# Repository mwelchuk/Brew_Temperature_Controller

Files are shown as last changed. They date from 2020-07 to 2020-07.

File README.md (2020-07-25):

# Brew Temperature Controller

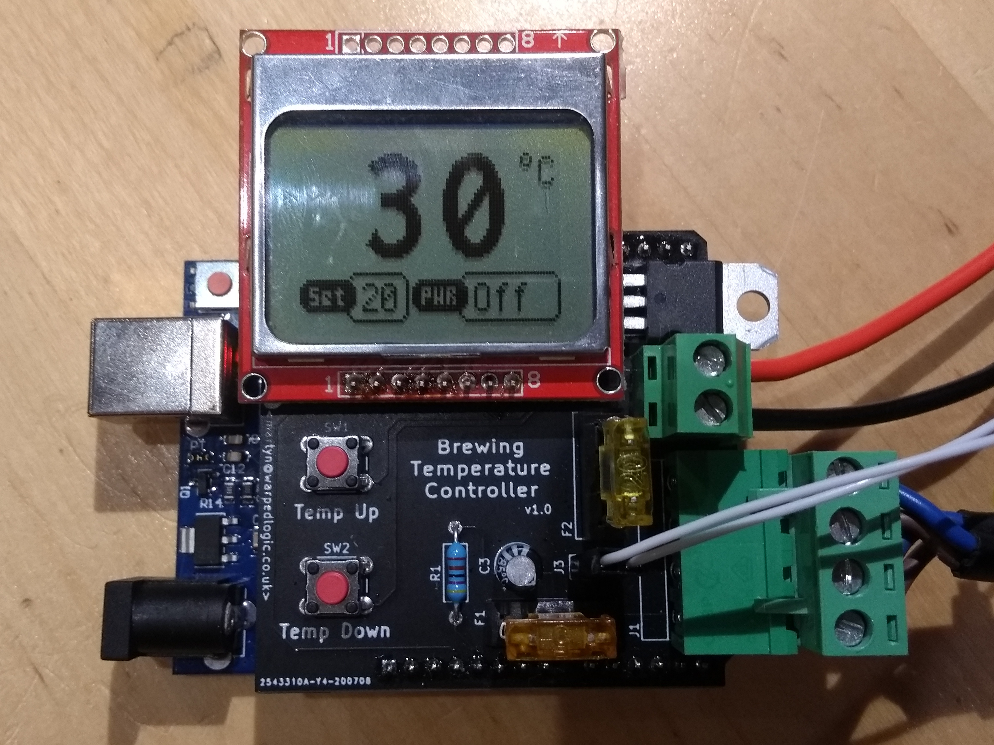
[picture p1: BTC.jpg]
Brew Temperature Controller


This project is a small heater controller that I have made to enable a few spare 3D printer parts I had lying arround to be used to control the temperature of my beer when brewing. I had been using a full RAMPS1.4 controller with a 4 line display, but this was very bulky. Rather than the Arduino Mega utilised with the RAMPS board, this uses an Arduino Uno, which is much smaller.

The device is fully powered from the PSU that's needed to supply power to the heater (this can not be pulled from the Arduino). If plugged in via USB, the set temperature, power output (scaled from 0-255) and current temperature are logged approximately once a second.

## PCB Ideas

- Improve layout of MOSFET now a more powerful transistor is being used.
- Getting noise back in (cheap) power supply, better smoothing?

## Code Ideas

- Better PID library

## Parts

- Parts below from CPC (cpc.farnell.com):

```
Order Code	Qty	Manufacturer Part Number	Manufacturer / Description									Line Price Ex. VAT (Inc. Vat)
SW02467		2	MCDTS6-1R			MULTICOMP PRO  Switch, Tactile 4.3mm 260g							0.22
CN21011		1	CTBP9358/4			CAMDENBOSS  5.08mm Horizontal Pluggable Terminal Block Header, 4-Pole, 15A			0.43
CN19453		1	CTB0708/2			CAMDENBOSS  PCB Terminal, High Power, 5.08mm, 2 Way						0.49
FF02092		2	MCCQ-122			MULTICOMP PRO  Fuseholder, PCB Mount, Mini Blade						0.48
CA08185		1	MCMR50V106M5X7			MULTICOMP PRO  Electrolytic Capacitor, 10 µF, 50 V, MCMR Series, ± 20%, Radial Leaded, 5 mm	0.05
SC11131		1	STP60NF06L			STMICROELECTRONICS  Power MOSFET, N Channel, 60 V, 60 A, 0.014 ohm, TO-220, Through Hole	1.36
```

- Nokia 5110 style screen with the following pinout:

```
Pin	Use
1	RST
2	CE
3	DC
4	DIN
5	CLK
6	VCC
7	LIGHT
8	GND
```

- Arduino Uno, cheap clone used
- Fuses: Standard Car mini Fuses. Used 5A (smallest I had) for electronics, 20A for heater output.
- Heater I found a standard 22cm circular 3D printer heated bed fits nicely under my brew bucket (it was this that inspired the build).
- Thermistor: Standard 100K thermistor, as used on many 3D printers.
- PSU: Currently using spare 0.8A 12v PSU as might be used on a small 3D printer.

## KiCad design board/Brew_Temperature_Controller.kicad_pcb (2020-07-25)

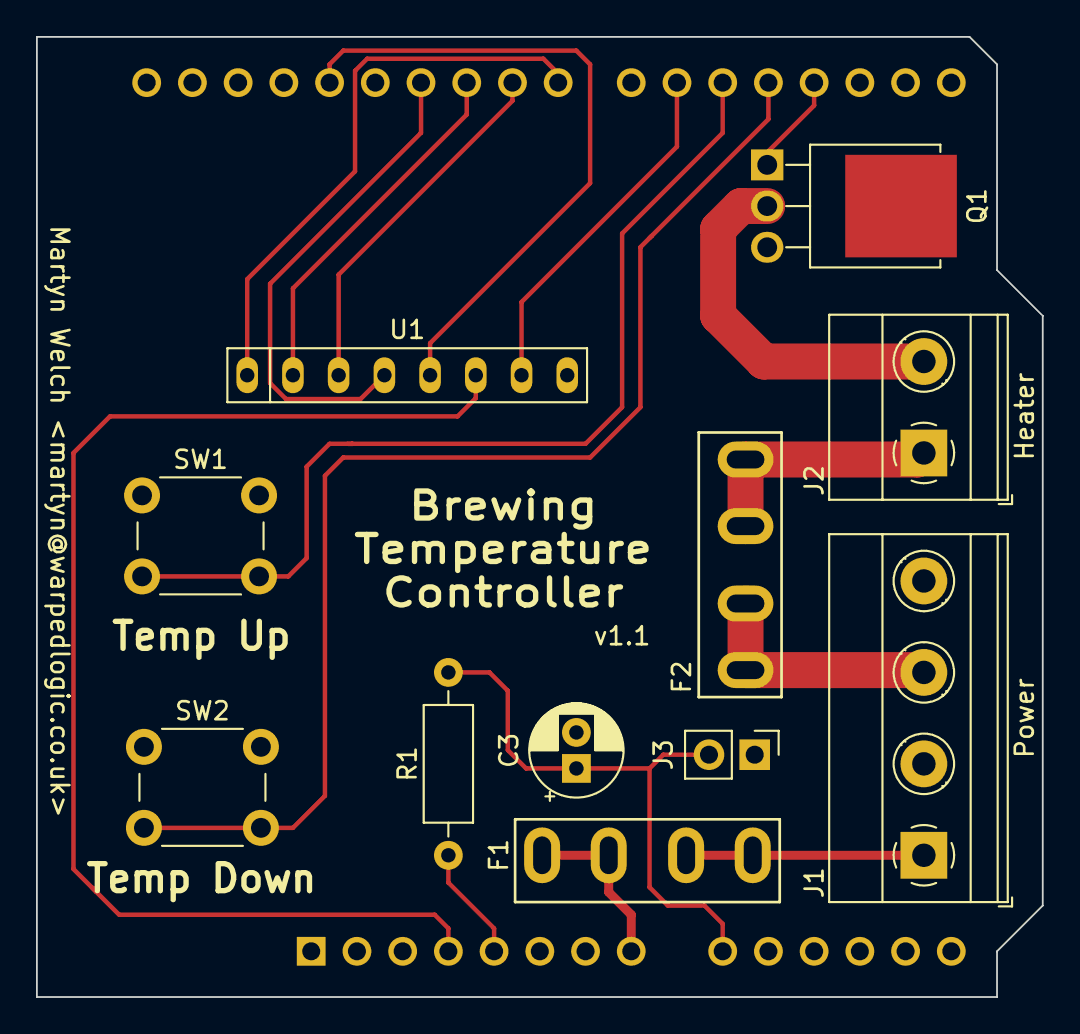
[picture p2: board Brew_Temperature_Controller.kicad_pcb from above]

Board: 2 copper layers, 55.9 x 53.3 mm, 12 parts (1 on the bottom side), 18 nets.

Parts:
A1: Arduino_UNO_R3
C3: 10uF; CP_Radial_D5.0mm_P2.00mm
F1, F2: MCCQ-122
J1: CTBP9358/4; TerminalBlock_Phoenix_MKDS-1,5-4-5.08_1x04_P5.08mm_Horizont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
J2: CTB0708/2; TerminalBlock_Phoenix_MKDS-1,5-2-5.08_1x02_P5.08mm_Horizont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
J3: Conn_01x02_Male; PinHeader_1x02_P2.54mm_Vertical
Q1: IRLU024NPBF; TO-251-3-1EP_Horizontal_TabDown
R1: 4K7; R_Axial_DIN0207_L6.3mm_D2.5mm_P10.16mm_Horizontal
SW1, SW2: MCDTS6-1R; SW_PUSH_6mm_H4.3mm
U1: Nokia_5110_Module

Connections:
+3V3: A1.4, U1.6
+5V: A1.5, R1.1
+12V: A1.8, F1.1
Button1: A1.20, SW1.2
Button2: A1.19, SW2.2
CE: A1.25, U1.2
DC: A1.24, U1.3
GND: A1.6, A1.7, A1.29, C3.2, J1.2, J1.4, J3.1, Q1.3, SW1.1, SW2.1, U1.8
HEATER: A1.18, Q1.1
LIGHT: A1.21, U1.7
unnamed: F1.2, J1.1
unnamed: F2.2, J1.3
unnamed: J2.2, Q1.2
RST: A1.23, U1.1
SCLK: A1.28, U1.5
SDIN: A1.26, U1.4
THERM: A1.9, C3.1, J3.2, R1.2
Vdrive: F2.1, J2.1

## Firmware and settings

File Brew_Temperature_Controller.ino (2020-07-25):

/*
 * Brewing Temperature Controller
 * 
 * Copyright (C) 2020 Martyn Welch <martyn@warpedlogic.co.uk>
 * 
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
 * You should have received a copy of the GNU General Public License
 * along with this program; if not, write to the Free Software
 * Foundation, Inc., 51 Franklin Street, Fifth Floor, Boston,
 * MA  02110-1301, USA.
 */

/*
 * The following libraries are used:
 * - NTC Thermistor (MIT): https://github.com/YuriiSalimov/NTC_Thermistor
 * - U8g2 (2-Clause BSD): https://github.com/olikraus/u8g2
 * - FastPID (LGPL v2.1): https://github.com/mike-matera/FastPID
 */

#include <Arduino.h>
#include <U8g2lib.h>
#include <Thermistor.h>
#include <NTC_Thermistor.h>
#include <FastPID.h>
#include <EEPROM.h>

#ifdef U8X8_HAVE_HW_SPI
#include <SPI.h>
#endif
#ifdef U8X8_HAVE_HW_I2C
#include <Wire.h>
#endif

#define SWITCH_1 5
#define SWITCH_2 4
#define THERM_PIN A0
#define LIGHT_PIN 6
#define OUTPUT_PIN 3

#define REFERENCE_RESISTANCE   4700
#define NOMINAL_RESISTANCE     100000
#define NOMINAL_TEMPERATURE    25
#define B_VALUE                3950

#define DEBOUNCE_PERIOD 1000

#define LIGHT_PERIOD 2000
unsigned long light_time = 0;

float Kp=25, Ki=0.2, Kd=0.01, Hz=37;
int output_bits = 8;
bool output_signed = false;

FastPID myPID(Kp, Ki, Kd, Hz, output_bits, output_signed);

U8G2_PCD8544_84X48_F_4W_SW_SPI u8g2(U8G2_R0, /* clock=*/ 13, /* data=*/ 11, /* cs=*/ 10, /* dc=*/ 9, /* reset=*/ 8);  // Nokia 5110 Display

unsigned long debounce_switch_1 = 0;
unsigned long debounce_switch_2 = 0;

#define SETMAX 40
#define SETMIN 0
int setpoint = 25;
char setchar[4];
#define NUM_TEMPS 20
double temps[NUM_TEMPS];
int temp_cnt = 0;
int current = 69;
char curchar[4];
uint8_t output = 0;
char outchar[5];
unsigned long log_time;

int state1;
int hold1 = 0;
bool change1 = true;

int state2;
int hold2 = 0;
bool change2 = true;

Thermistor* thermistor;

#define SAVE_MAGIC 0xbe
#define SAVE_ADDRESS 0
struct saved_state {
  int magic;
  int temp;
};

struct saved_state saved;

void setup(void) {

  u8g2.begin();

  Serial.begin(115200);

  pinMode(SWITCH_1, INPUT_PULLUP);
  pinMode(SWITCH_2, INPUT_PULLUP);
  pinMode(LIGHT_PIN, OUTPUT);
  digitalWrite(LIGHT_PIN, HIGH);
  pinMode(OUTPUT_PIN, OUTPUT);
  digitalWrite(OUTPUT_PIN, LOW);

  thermistor = new NTC_Thermistor(
    THERM_PIN,
    REFERENCE_RESISTANCE,
    NOMINAL_RESISTANCE,
    NOMINAL_TEMPERATURE,
    B_VALUE
  );

  Serial.println("Setpoint, Output, Temperature");

  EEPROM.get(SAVE_ADDRESS, saved);

  if (saved.magic == SAVE_MAGIC) {
    setpoint = saved.temp;
  } else {
    saved.magic = SAVE_MAGIC;
  }

}

/*
uint8_t bitmap[] = {0x3F, 0xFF, 0xA5, 0xA5, 0xA1, 0xE1, 0x21, 0x1E};
*/
void refresh_display(char *curchar, char *setchar, char *powerchar) {
  // Write current temp and units
  u8g2.clearBuffer();
  u8g2.setFont(u8g2_font_inb30_mf);
  u8g2.drawStr(18, 30, curchar);
  u8g2.setFont(u8g2_font_profont12_tf);
  u8g2.drawGlyph(70, 10, 176);
  u8g2.drawStr(77, 10, "C");

  // Draw set temp box
  u8g2.drawRFrame(15, 34, 20, 14, 3);
  u8g2.drawRBox(0, 36, 18, 9, 3);
  u8g2.setFont(u8g2_font_micro_tr);
  u8g2.setDrawColor(0);
  u8g2.drawStr(3, 43,"Set");
  u8g2.setDrawColor(1);

  // Draw power box
  u8g2.drawRFrame(51, 34, 33, 14, 3);
  u8g2.drawRBox(36, 36, 18, 9, 3);
  u8g2.setFont(u8g2_font_micro_tr);
  u8g2.setDrawColor(0);
  u8g2.drawStr(39, 43,"PWR");
  u8g2.setDrawColor(1);

  // Power state and set temp
  u8g2.setFont(u8g2_font_profont12_tf);
  u8g2.drawStr(56, 45, powerchar);
  u8g2.drawStr(20, 45, setchar);
/*
  // Beer Mug Graphic
  u8g2.drawBitmap(0,0,1,8,bitmap);
*/
  // Transfer buffer to the display
  u8g2.sendBuffer();
}


void loop(void) {
  unsigned long now;
  int state;
  double tot = 0;
  double avg_temp;
  char pwrchar[4];
  double current;
  uint8_t pcnt;

  now = millis();
  
  state = digitalRead(SWITCH_1);
  if (state == state1) {
    if ((now - debounce_switch_1) < DEBOUNCE_PERIOD) {
      if ((state == 0) & (change1 == true)) {
        if (setpoint < SETMAX)
          setpoint++;
        change1 = false;

      }
      debounce_switch_1 = now;
      hold1++;
      if ((state == 0) & (hold1 > 10))
        if (setpoint < SETMAX)
          setpoint++;

      if (state == 0) {
        light_time = now;
        digitalWrite(LIGHT_PIN, LOW);
      }
    }
  } else {
    debounce_switch_1 = now;
    state1 = state;
    change1 = true;
    hold1 = 0;
  }
  
  state = digitalRead(SWITCH_2);
  if (state == state2) {
    if ((now - debounce_switch_2) < DEBOUNCE_PERIOD) {
      if ((state == 0) & (change2 == true)) {
        if (setpoint > SETMIN)
          setpoint--;
        change2 = false;
      }
      debounce_switch_2 = now;
      hold2++;
      if ((state == 0) & (hold2 > 10))
        if (setpoint > SETMIN)
          setpoint--;

      if (state == 0) {
        light_time = now;
        digitalWrite(LIGHT_PIN, LOW);
      }
    }
  } else {
    debounce_switch_2 = now;
    state2 = state;
    change2 = true;
    hold2 = 0;
  }

  saved.temp = setpoint;
  EEPROM.put(SAVE_ADDRESS, saved);

  if (now - light_time > LIGHT_PERIOD)
    digitalWrite(LIGHT_PIN, HIGH);

  current = thermistor->readCelsius();
  temps[temp_cnt++] = current;
  temp_cnt = temp_cnt % 20;

  for (int i=0; i < NUM_TEMPS; i++)
    tot += temps[i];

  output = myPID.step(setpoint, current);

  avg_temp = tot / NUM_TEMPS;

  if (avg_temp < 0) {
    sprintf(curchar, "XX");
  } else {
    sprintf(curchar,"%d", round(avg_temp));
  }

  itoa(setpoint, setchar, 10);

  if (output > 255)
    output = 255;

  /* Protect against unplugged or broken temp sensor */
  if (current < 0) {
    output = 0;
  }

  analogWrite(OUTPUT_PIN, output);

  pcnt = (output * 100) / 255;
  if (output == 0) {
    sprintf(outchar, "Off");
  } else {
    sprintf(outchar,"%d%%", pcnt);
  }

  refresh_display(curchar, setchar, outchar);

  /* Limit logging rate */
  if (now - log_time > 1000) {
    log_time = log_time + 1000;
    Serial.print(setpoint);
    Serial.print(", ");
    Serial.print(output);
    Serial.print(", ");
    Serial.println(current);
  }
}

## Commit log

2020-07-25 Initial code start at code implementation
    This code is not complete, but a first test state:
    - Screen working and layout almost complete
    - Temp set point buttons function (still needs limits)
    - Temperature sensor working
    - Integration of PID loop underway
    [Brew_Temperature_Controller-B_Cu.gbr, Brew_Temperature_Controller-B_Mask.gbr, Brew_Temperature_Controller-Edge_Cuts.gbr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]
2020-07-25 Board tweaks and software update
    The use of D2 to control the heater was a mistake as it does not
    provide PWM, switch to using D3.
    The chosen MOSFET was not suitable for driving the heater at full
    current and has thus been switched for a more powerful one.
    Move the README so that it's more general for the whole project rather
    than just the board design and use Markdown.
    Add license to source code.
    Add features to the software:
    - Drive output with PWM
    - Utilise screen backlight
    - Save set temperature across boots
    - Display percentage power output when on
    - Test for detached thermistor and turn off output as safety measure
    - Allow scrolling of setpoint with long press of buttons
    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
    [Brew_Temperature_Controller.kicad_pcb, Brew_Temperature_Controller.sch]

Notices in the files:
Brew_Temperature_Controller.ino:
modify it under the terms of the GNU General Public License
